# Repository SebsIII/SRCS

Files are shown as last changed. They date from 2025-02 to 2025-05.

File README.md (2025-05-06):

# SRCS - Satellite Receiver Control Station

The Satellite Receiver Control Station (SRCS) is an operational facility dedicated to maximizing the quality and reliability of satellite signal reception. This is achieved through the continuous acquisition, processing, and analysis of diverse sensor data streams. The SRCS leverages this information to dynamically optimize antenna pointing, receiver parameters, and other system configurations, ensuring optimal signal capture and data integrity.

## Description
The control station is made primarely of 2 modules:
- The motorized antenna module : The **core** of the control station and the actual receiver, it's composed of a [Vee dipole antenna](https://en.wikipedia.org/wiki/Dipole_antenna) tuned at NOAA's frequencies in horizontal polarization and connected to a [28BYJ-48](https://www.mouser.com/datasheet/2/758/stepd-01-data-sheet-1143075.pdf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) stepper motor, which handles it's ability to rotate the antenna to track satellites.
- The weather data module - The secondary part of the SRCS that gathers weather data that will be analyzed by the [MCU](https://en.wikipedia.org/wiki/Microcontroller) and saved on an external database.
## 🛰️ The NOAA's satellites

The NOAA ([National Oceanic Atmospheric Atministration](https://www.noaa.gov/)) is a US  agecy that studies how weather changes our planet, both on it's surface and under the seas. <br>
Other then other missions, it made a [campaign of polar-orbiting, non-geosynchronous, environmental satellites](https://www.n2yo.com/satellites/?c=4), from NOAA-1 up to NOAA-21. <br>
From all of those, the best and easiest one to receive are the NOAA-15, NOAA-18 and NOAA-19, which continously trasmit weather data with [APT](https://en.wikipedia.org/wiki/Automatic_picture_transmission) techniques on their downlink frequency as a "sound". <br>
Those "sounds" will eventually need to be converted into .WAV files and thed decoded with an apt-decoder, in our case we'll use [noaa-apt](https://noaa-apt.mbernardi.com.ar/).

<table>
<tr><td>Name</td><td>NORAD ID</td><td>Freq MHz</td></tr>
<tr><td>NOAA 15</td><td><a href="https://www.n2yo.com/satellite/?s=25338">25338</a></td><td>137.620</td></td></tr>
<tr><td>NOAA 18</td><td><a href="https://www.n2yo.com/satellite/?s=28654">28654</a></td><td>137.9125</td></tr>
<tr><td>NOAA 19</td><td><a href="https://www.n2yo.com/satellite/?s=33591">33591</a></td><td>137.1</td></tr>
</table>

## 1st Module: The Vee Dipole Antenna

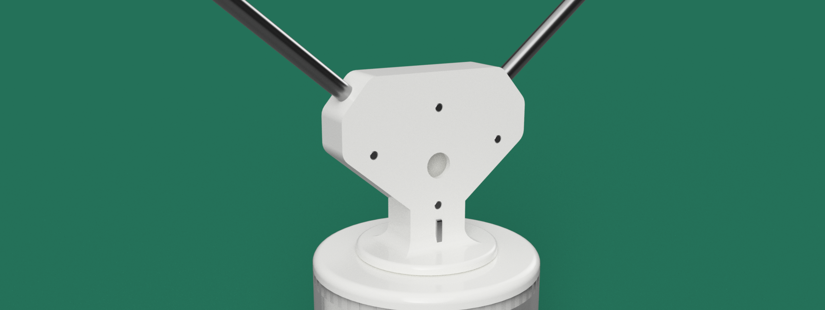
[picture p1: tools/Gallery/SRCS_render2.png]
Vee antenna


The first module is made of two parts, the **dipole antenna** and the **motorized support**:
- The dipole antenna is the effective receiver of the SRCS, it's a horizontally polazied, omnidirectional, **Vee dipole antenna** tuned at 137.25 MHz (average downlink frequency of NOAA-15,18,19 *). <br>
  The antenna output will eventually be connected to a 50 ohm [RG58 coaxial cable](https://www.farnell.com/datasheets/2095749.pdf) that will transfer the output signal from the antenna to the [RTL-SDR](https://en.wikipedia.org/wiki/Software-defined_radio) or the general receiver that will, later on, analyze the signal and convert it in an image. <br>
  
- The motorized support is where the antenna is mounted and the part that will, indeed, **rotate** the antenna itself while the satellite is passing near the SRCS 
  to ensure the highest quality receiving of data reception of the dipole. <br>
  Its mainly composed of a [28BYJ-48 stepper motor](https://www.mouser.com/datasheet/2/758/stepd-01-data-sheet-1143075.pdf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), a **5.625:1 gear box** to reduce the motor speed and to reduce the minimum step angle and an [AS5600 magnetic encoder](https://files.seeedstudio.com/wiki/Grove-12-bit-Magnetic-Rotary-Position-Sensor-AS5600/res/Magnetic%20Rotary%20Position%20Sensor%20AS5600%20Datasheet.pdf) to get the exact rotation angle of the dipole.
  
<h6>* The bandwidth of the 137.25 MHz dipole antenna offers enough bandwindth to get all the 137.1, 137.620 and 137.9125 MHz frequencies </h6>

## 2nd Module: Weather data Module

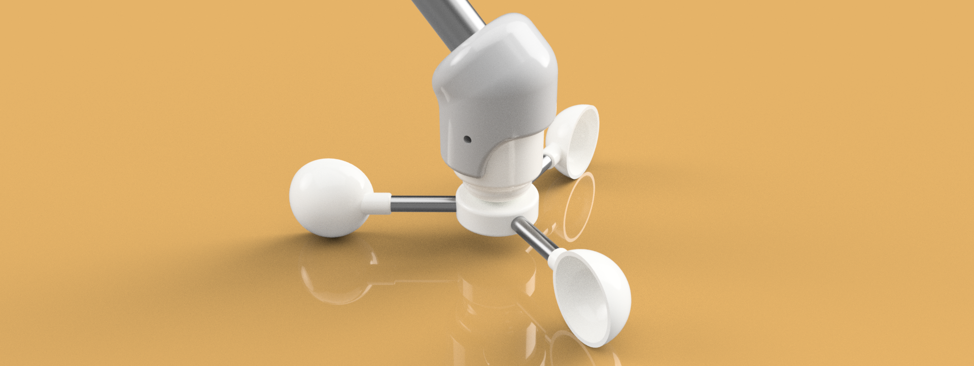
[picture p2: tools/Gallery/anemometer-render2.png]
anemometer


The second module is the weather monitor system, which is the part which goal is to gather weather data that will later on, be analyzed by the MCU.
It's composed of various sensors, including: [DHT11]() for **temperature and humidity**, a light sensor, to gather **ambient light level**, an anemometer for **wind speed** and a rain sensor. <br>
The combination of those data, will be used to **monitor and predict how currend and future weather is/will be**. <br>
Those info are necessary to better understand how the weather will be during the NOAA receiving sessions, since those conditions can impact on the reciving quality and/or damage some components if used under certain situations, like rain or extreme wind storms.

## The Power Managment System PMS

The SRCS is powered by a **9v 5w solar panel** which charges up a **12v 7AH Lead acid battery** with a **[XY-L10A](https://www.google.com/url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) BMS** which handles and manages the battery charging-sequencies.
Before the BMS, there's a **buck step-up circuit** which up-shifts the voltage from *9v => ~13v*, needed to charge the battery.
The battery outputs are then inputted in two **buck step-down circuits**, one at *~7,5v for the MCU power supply* and the other at *5v for the sensors power supply*.

The complete system is schematized below:

``` 
Solar panel
    |        
    v        
   13v---> XY-L10A
    |        v
    v        |
 Battery <---/
  |   |
  v   v
 7.5v 5v--> Sensors IN 
  |
  v   
STM32F401RE VIN
```

## The communication protocol

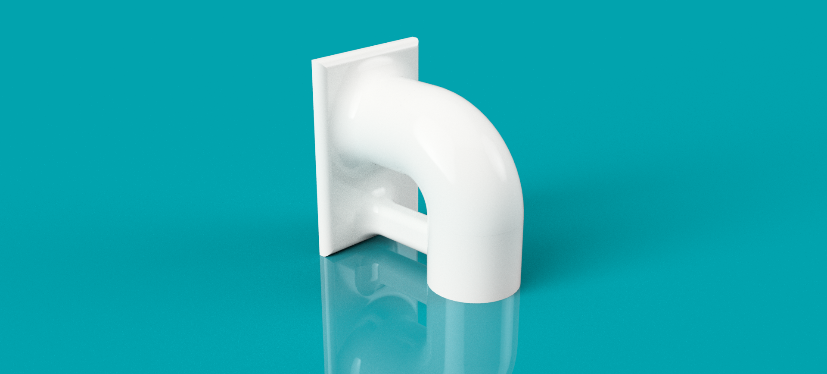
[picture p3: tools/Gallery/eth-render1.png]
dashboard-overview


The SRCS, other than a control station is also a **web server** hosting a **local website**, on which are displayed the weather data, the SRCS status, the nearby satellite passes data and much more.
 
The website is written in **HTML**,**CSS** and **JS** and the communication protocol between the website and the SRCS itself is based on [AJAX](https://en.wikipedia.org/wiki/Ajax_(programming)).

The **website local IP address** is set to:
```
http://192.168.1.100
```

## Usage

When you want to start a new reception session, click the **Start reception session** button, a login pop-up will show up, in this, you will need to insert the password to continue. 

If the password is right, a new pop-up will show up, requesting the **command info to send to the SRCS**, The command is in this format:
``` 
Rotate [from] degrees => [to] degrees in [for] seconds, [after] seconds
```

here's an *example* to better understand how the command format works:
> Rotate from 0° => to 180°, in 600s, after 900s 

With this command, the SRCS will **align and rotate the antenna from 0° [North] to 180° [south] in 10 min, after 15min after the reception of the command**.

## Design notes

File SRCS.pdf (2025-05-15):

Cutillo Sebastiano Maria - A.S. 2024/2025

## SRCS - Satellite Receiver Control Station

https://github.com/SebsIII/SRCS

La Satellite Receiver Control Station (SRCS) è una struttura operativa dedicata a massimizzare la qualità e l'affidabilità della ricezione dei segnali satellitari. Questo obiettivo viene raggiunto attraverso l'acquisizione, l'elaborazione e l'analisi continua di diversi flussi di dati da sensori.

La SRCS sfrutta queste informazioni per ottimizzare dinamicamente il puntamento dell'antenna, i parametri del ricevitore e altre configurazioni del sistema, garantendo la cattura ottimale del segnale e l'integrità dei dati.

Descrizione

La stazione di controllo è composta principalmente da 2 moduli:

- Il modulo antenna motorizzata: il cuore della stazione di controllo e del ricevitore vero e proprio, è composto da un'antenna dipolo Vee sintonizzata sulle frequenze NOAA in polarizzazione orizzontale e collegata a un motore passo-passo 28BYJ-48, che ne gestisce la capacità di ruotare l'antenna per seguire i satelliti.
- Il modulo dati meteo - La parte secondaria dell'SRCS che raccoglie i dati meteo che saranno analizzati dalla MCU e salvati su un database esterno.

I satelliti NOAA

La NOAA (National Oceanic Atmospheric Atministration) è un'agenzia statunitense che studia come le condizioni meteorologiche modificano il nostro pianeta, sia sulla superficie che sotto i mari. Oltre ad altre missioni, ha realizzato una campagna di satelliti ambientali in orbita polare, non geosincroni, dal NOAA-1 fino al NOAA-21.

Di tutti questi, i migliori e più facili da ricevere sono i NOAA-15, NOAA-18 e NOAA-19, che trasmettono continuamente dati meteorologici con tecniche APT sulla loro frequenza di downlink come “suono”.

Questi “suoni” dovranno essere convertiti in file .WAV e decodificati con un decodificatore apt.

1° Modulo: L'antenna a dipolo Vee

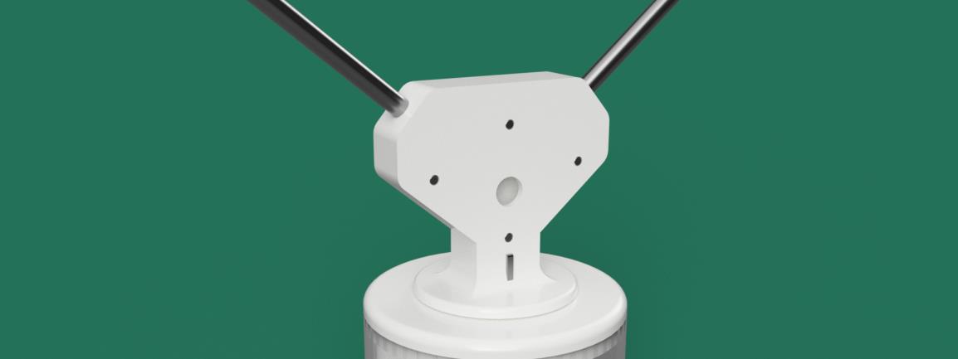
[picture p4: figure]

Il primo modulo è composto da due parti, l'antenna a dipolo e il supporto motorizzato:

- L'antenna a dipolo è il ricevitore effettivo dell'SRCS; si tratta di un'antenna a dipolo Vee, omnidirezionale e polarizzata orizzontalmente, sintonizzata a 137,25 MHz (frequenza media di downlink delle NOAA-15,18,19 *). L'uscita dell'antenna sarà infine collegata a un cavo coassiale RG58 da 50 ohm che trasferirà il segnale in uscita dall'antenna all'RTL-SDR o al ricevitore generale che, in seguito, analizzerà il segnale e lo convertirà in un'immagine.
- Il supporto motorizzato è il punto in cui viene montata l'antenna e la parte
che, di fatto, ruoterà l'antenna stessa mentre il satellite passa vicino all'SRCS per garantire la massima qualità di ricezione dei dati del dipolo. È composto principalmente da un motore passo-passo 28BYJ-48, una scatola di ingranaggi 5,625:1 per ridurre la velocità del motore e ridurre l'angolo di passo minimo e un encoder magnetico AS5600 per ottenere l'angolo di rotazione esatto del dipolo.

* La larghezza di banda dell'antenna a dipolo da 137,25 MHz offre una banda sufficiente per ottenere tutte le frequenze di 137,1, 137,620 e 137,9125 MHz.

2° Modulo: Modulo dati meteo

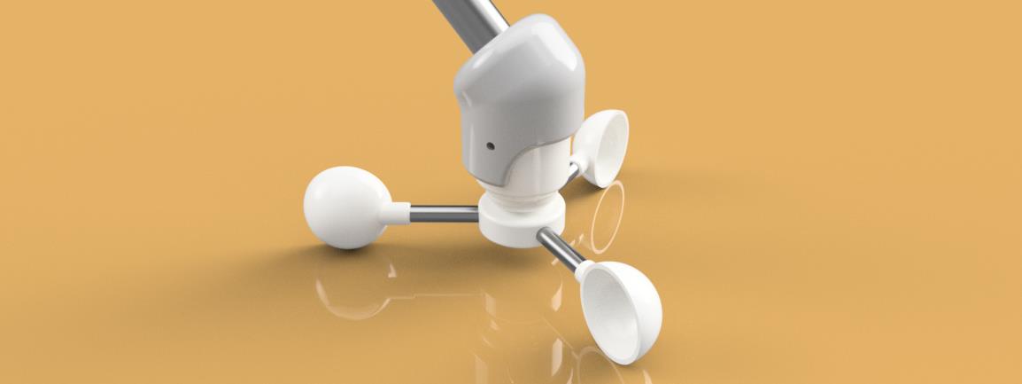
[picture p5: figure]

Il secondo modulo è il sistema di monitoraggio meteorologico, ovvero la parte che ha lo scopo di raccogliere i dati meteorologici che saranno poi analizzati dall'MCU. È composto da vari sensori, tra cui: DHT11 per la temperatura e l'umidità, un sensore di luminosità, per raccogliere il livello di luce ambientale, un anemometro per la velocità del vento e un sensore di pioggia.

La combinazione di questi dati sarà utilizzata per monitorare e prevedere l'andamento e le condizioni meteorologiche future.

Queste informazioni sono necessarie per comprendere meglio le condizioni meteorologiche che si verificheranno durante le sessioni di ricezione NOAA, poiché tali condizioni possono influire sulla qualità della ricezione e/o danneggiare alcuni componenti se utilizzati in determinate situazioni, come pioggia o tempeste di vento estreme.

Il sistema di gestione dell'energia PMS

Il sistema di gestione dell'alimentazioneL'SRCS è alimentato da un pannello solare da 9v 5w che carica una batteria al piombo da 12v 7AH con un BMS XY-L10A che gestisce le sequenze di carica della batteria. Prima del BMS, c'è un circuito buck step-up che aumenta la tensione da 9v => ~13v, necessaria per caricare la batteria. Le uscite della batteria vengono poi immesse in due circuiti buck step-down, uno a ~7,5v per l'alimentazione della MCU e l'altro a 5v per l'alimentazione dei sensori.em PMS

Il protocollo di cominicazione

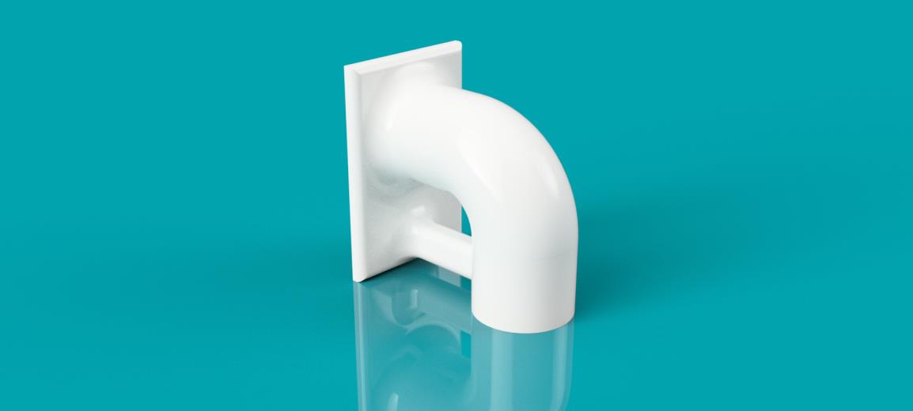
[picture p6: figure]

L'SRCS, oltre a essere una stazione di controllo, è anche un server web che ospita un sito web locale, sul quale vengono visualizzati i dati meteo, lo stato dell'SRCS, i dati dei passaggi dei satelliti nelle vicinanze e molto altro.

Il sito web è scritto in HTML, CSS e JS e il protocollo di comunicazione tra il sito web e l'SRCS stesso è basato su AJAX.

L'indirizzo IP locale del sito è impostato su: 192.168.1.100

Utilizzo

Quando si desidera avviare una nuova sessione di ricezione, fare clic sul pulsante Avvia sessione di ricezione; viene visualizzato un pop-up di accesso, in cui è necessario inserire la password per continuare.

Se la password è corretta, viene visualizzato un nuovo pop-up che richiede le informazioni sul comando da inviare all'SRCS:

Ruota [da] gradi => [a] gradi in [per] secondi, [dopo] secondi

Ecco un esempio per capire meglio come funziona il formato del comando:

Ruota da 0° => a 180°, in 600s, dopo 900s

Con questo comando, l'SRCS allineerà e ruoterà l'antenna da 0° [nord] a 180° [sud] in 10 minuti, dopo 15 minuti dalla ricezione del comando.

GitHub

Per maggiori informazioni, il codice completo, le immagini ed altro, il progetto si trova su GitHub al link: https://github.com/SebsIII/SRCS

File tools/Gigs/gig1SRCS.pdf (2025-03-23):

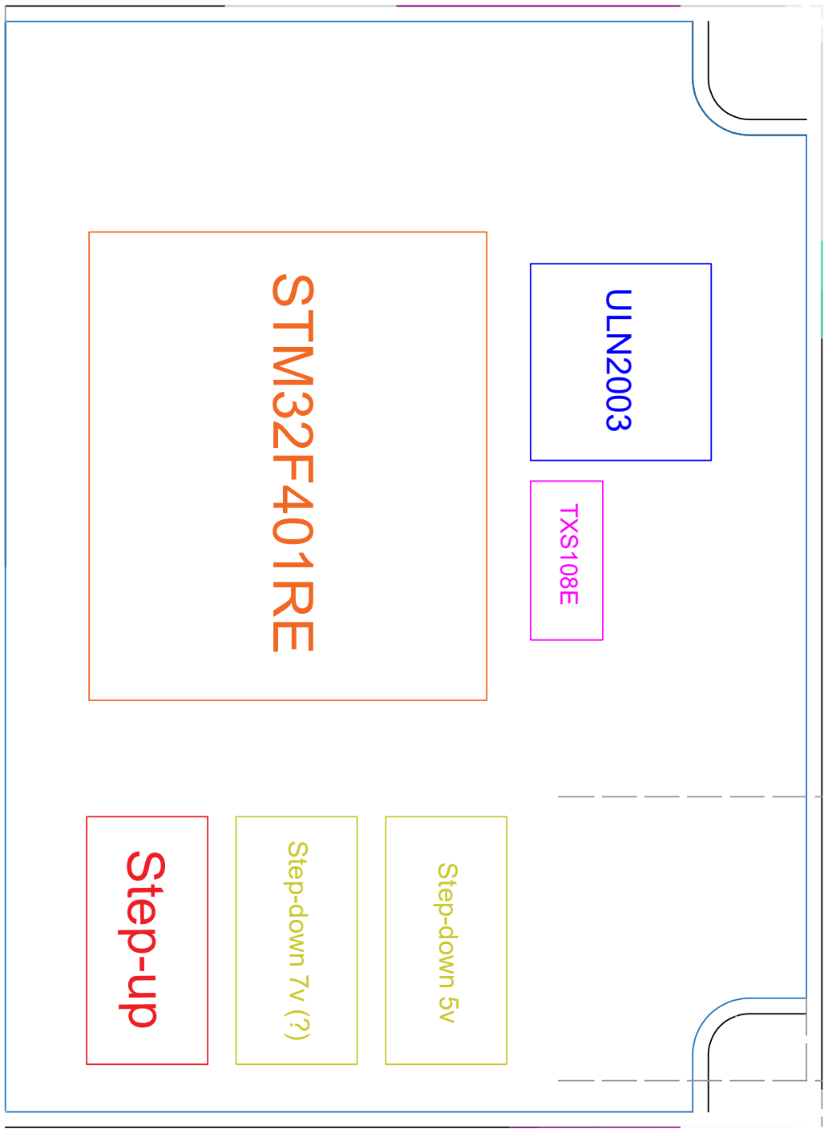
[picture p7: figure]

STM32F401RE Step-up Step-down 7v (?) Step-down 5v ULN2003 TXS108E

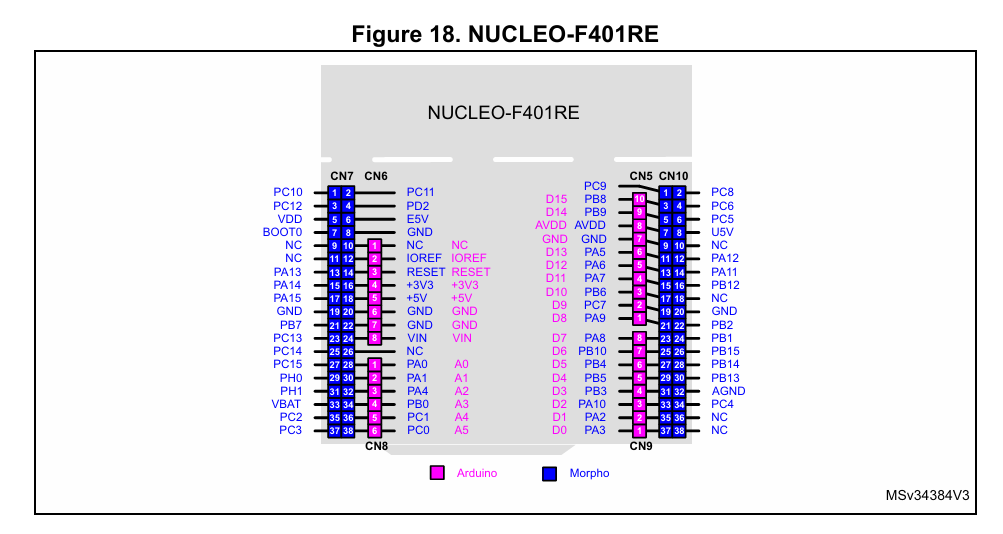
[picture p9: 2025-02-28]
datasheets/F401RE-pinout.png

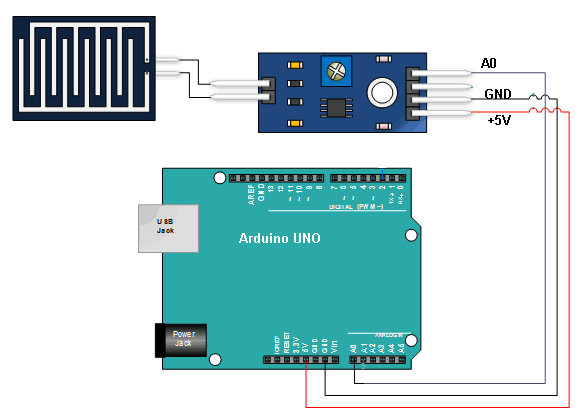
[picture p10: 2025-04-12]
wireups/Rain-sensor-wireup.png

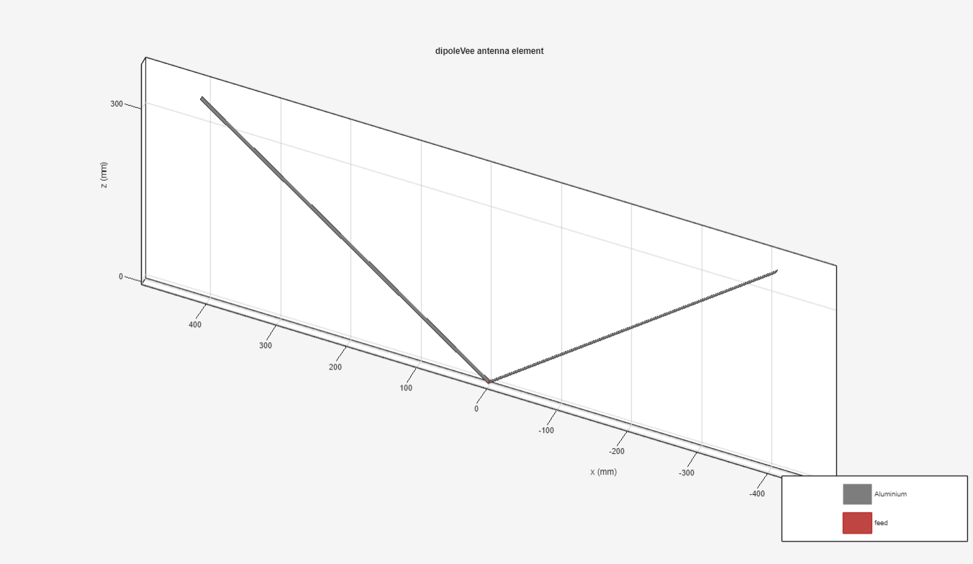
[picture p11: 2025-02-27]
datasheets/Vee-antenna/antenna-V.png

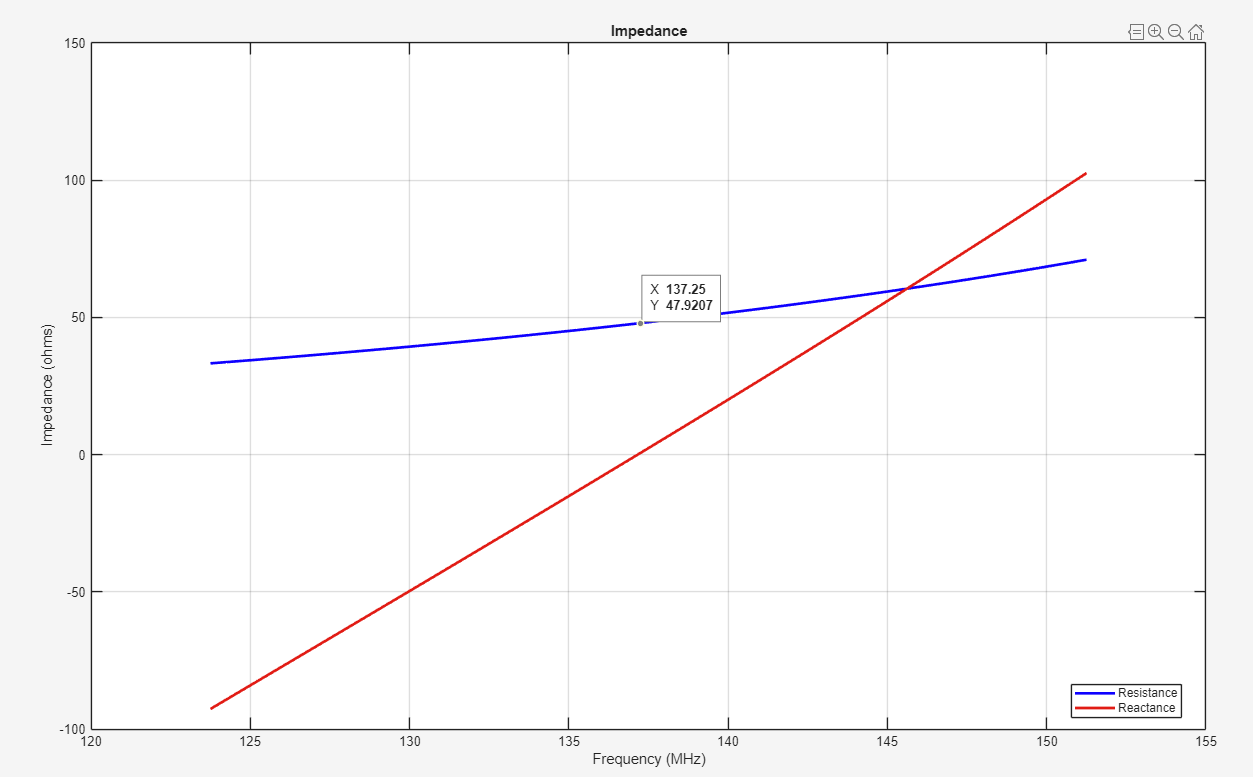
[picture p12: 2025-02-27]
datasheets/Vee-antenna/impedance.png

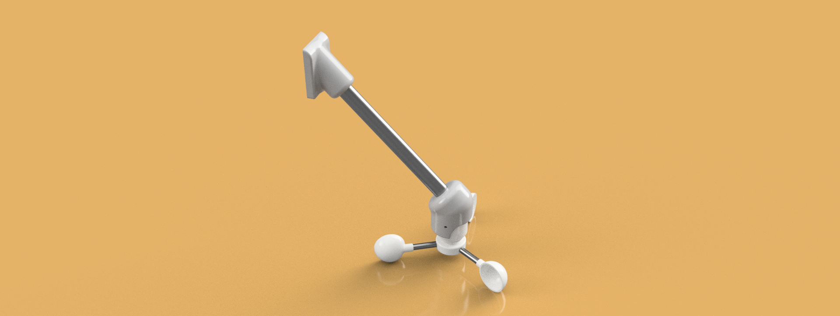
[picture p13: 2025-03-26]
tools/Gallery/anemometer-render1.png

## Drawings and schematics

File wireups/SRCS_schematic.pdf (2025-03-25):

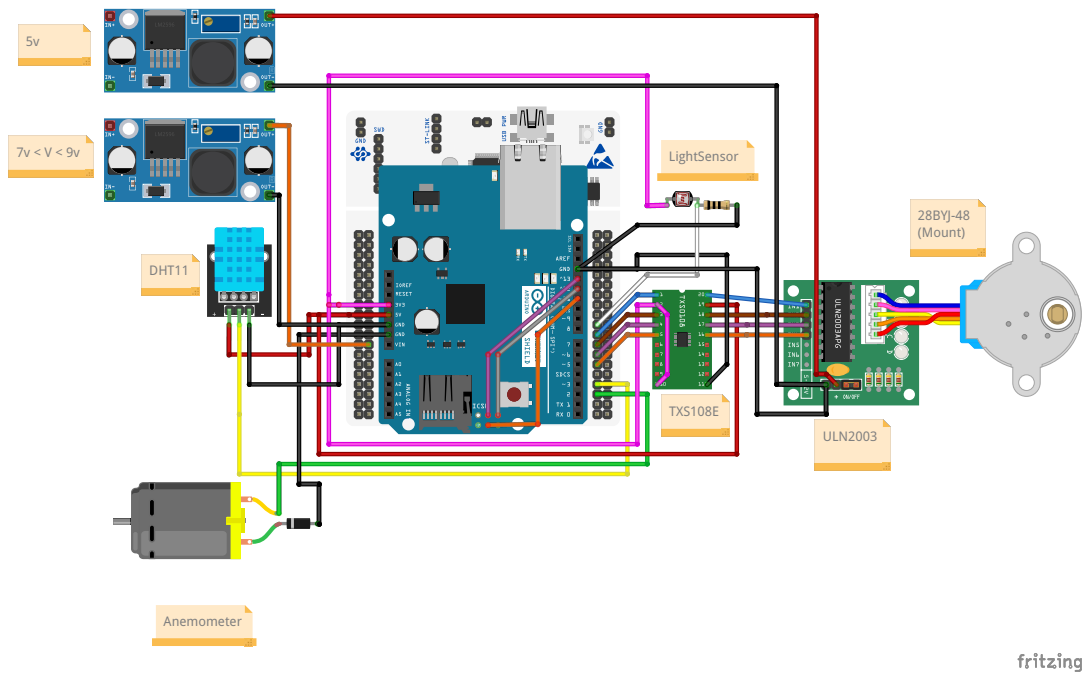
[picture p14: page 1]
Anemometer; DHT11; LightSensor; TXS108E; ULN2003; 28BYJ-48 (Mount)

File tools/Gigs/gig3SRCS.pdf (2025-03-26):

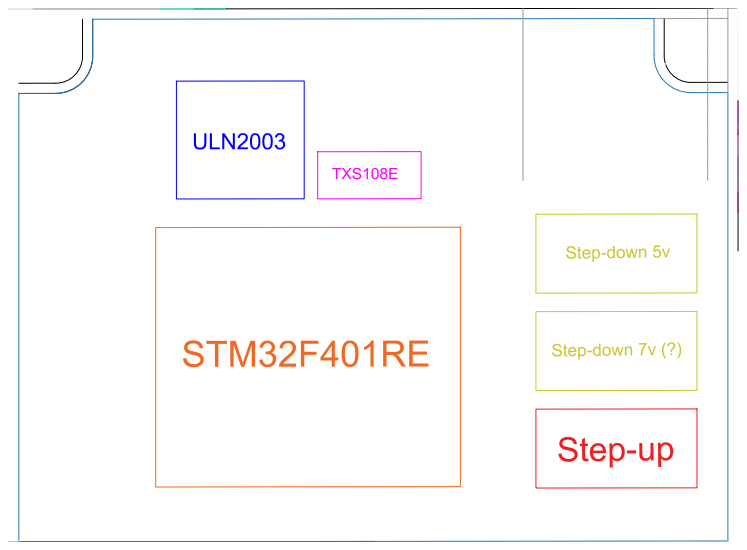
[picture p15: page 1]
STM32F401RE; Step-up Step-down 7v (?) Step-down 5v ULN2003; TXS108E

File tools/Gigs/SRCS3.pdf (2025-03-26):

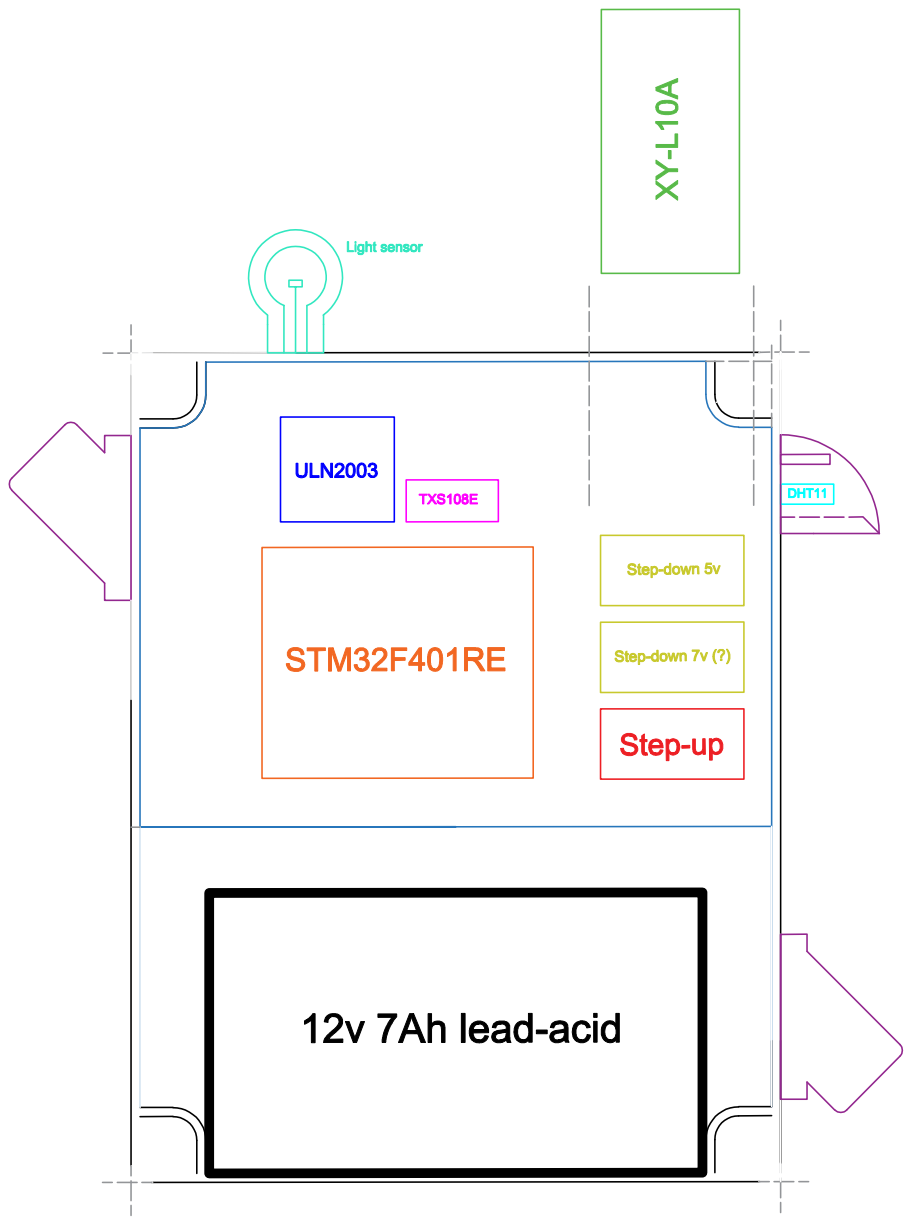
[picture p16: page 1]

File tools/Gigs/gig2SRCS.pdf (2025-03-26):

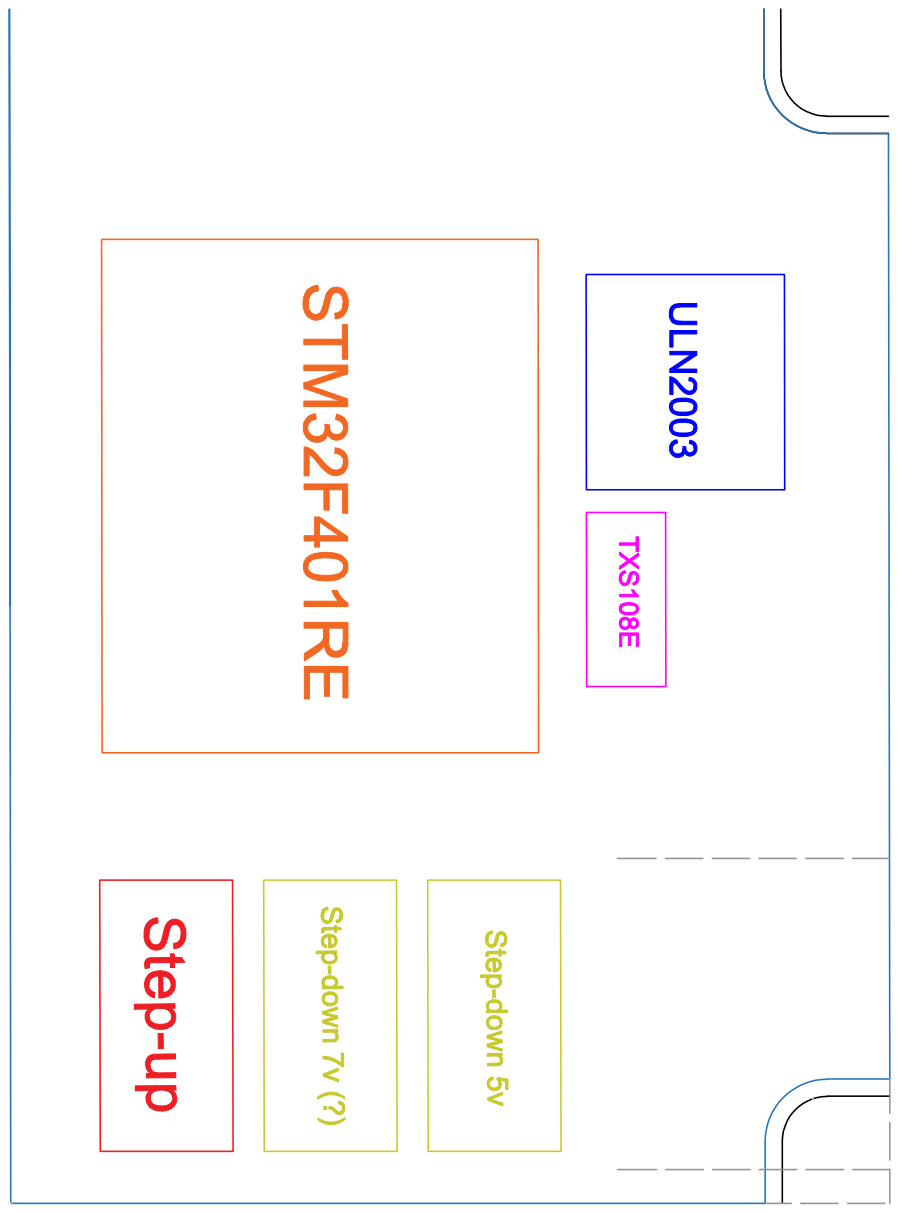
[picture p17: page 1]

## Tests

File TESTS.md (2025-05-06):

# SENSORS' TESTS

- [X] TXS0108E
- [x] 28BYJ-48
- [x] ULN2003
- [X] rain sensor
- [X] DHT11 - OK
- [X] Photoresistor
- [X] W5100 

## WIREUPS

- [X] [STM32 TO ARDUINO IDE](https://www.youtube.com/watch?v=yssEiMLGH90)
- [X] [DHT11](https://randomnerdtutorials.com/esp32-dht11-dht22-temperature-humidity-sensor-arduino-ide/), adapted
- [X] [STM32 to Ethernet shield](https://balau82.wordpress.com/2015/08/02/arduino-ethernet-shield-on-stm32-nucleo/)
- [ ] [AJAX](https://startingelectronics.org/tutorials/arduino/ethernet-shield-web-server-tutorial/web-server-read-switch-using-AJAX/)
- [X] [Ajax sd web](https://www.youtube.com/watch?v=E3uCFFf3hxc)

## Snippets

Pin Format: NAMEPIN

### DHT11

``` cpp
float getTemperature(){
  float T = dht.readTemperature();
  if (isnan(T)) {   
    return 0;
  }
  return  T;
}
```
``` cpp
float getHumidity(){
  float H = dht.readHumidity();
  if (isnan(H)) {   
    return 0;
  }
  return  H;
}
```

## Rain Sensor
``` cpp
int getRain(){  //To format raw input 
  int RL = analogRead(RAINPIN);
  return  RL;
}
```

## Light Sensor
``` cpp
int getLight(){  //To format raw input 
  int LL = analogRead(PHOTOPIN);
  return  LL;
}
```

## Anemometer
``` cpp
float getWind(){  //To format raw input (?)
  int WS = analogRead(ANEMOPIN);
  return  WS;
}
```

## Rain A => value
- 1020~1023 = clear
- 1019~800 = some droplets
- 799~600 = rain
- 599~50 = heavy rain
- 50~0 = metal on the sensor

## Web datasheet
- **AA** - Antenna Azimuth
- **AD** - [Last] Antenna Direction
- **MApDR** - Maximum Angle per Direction (of) Rotation [left]
- **Rain** - Rain Level
- **POST** - [Last] Power On Self Test [Outcome]
- **MRC** - Meteorological Reliability Coefficient

## Web data
- font - [Questial, allura, Oswald]

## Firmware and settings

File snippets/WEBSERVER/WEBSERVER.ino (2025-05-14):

/*
  SRCS basecode by Sebs_

  This is the source code for SRCS MCU, it handles HTTPreq from clients,
  stores and hosts a web server and does calculations in order to get,
  analyze and send the sensors' data to each client.

  Documentation and assets: https://github.com/SebsIII/SRCS

*/
#include <SPI.h>
#include <Ethernet.h>
#include <SD.h>
#include <DHT.h>
#include "AS5600.h"
#include <Stepper.h>

#define DHTPIN 3
#define DHTTYPE DHT11

#define PHOTOPIN A0
#define RAINPIN A1 
#define ANEMOPIN A2

AS5600 as5600;
Stepper mount(64, 8,6,7,5);
DHT dht(DHTPIN, DHTTYPE);
File HMTL_file, pswLog_file;

String psw, pswAttempt, alignCmmd;
int align_from = -1, align_to = -1, align_for =-1, align_after = -1, from_value, to_value, for_value, after_value ;
int startPoint, endPoint;
int dataArray[4];
float weatherData[5];
bool haveJob = false;
unsigned long instantTime, lastTrigger = 0, jobTime;
int isClockwise = 1; //1 = counter clock-wise, -1 = clok-wise
byte mac[] = {
  0xDE, 0xAD, 0xBE, 0xEF, 0xFE, 0xED
};
IPAddress ip(192, 168, 1, 100); 
EthernetServer server(80);

void setup()
{
  Serial.begin(115200);
  pinMode(PHOTOPIN, INPUT);
  pinMode(RAINPIN, INPUT);
  pinMode(ANEMOPIN, INPUT);
  if(!POST()){
    Serial.println("POST FALSE");
    while (true){};
  }
  
  pswLog_file = SD.open("psw.txt");
  while (pswLog_file.available()){
    psw += (char)pswLog_file.read();
  }

}

void loop()
{
  String HTTP_req;
  EthernetClient client = server.available();
  
  if(client)
  {
    boolean currentLineIsBlank = true;
    while (client.connected())
    {
      instantTime = millis()/1000;
      if(instantTime%1 == 0 && instantTime != lastTrigger){
        lastTrigger = instantTime;
        checkAndExecJob();
      }
      
      if(client.available())
      { 
        char c = client.read();
        HTTP_req += c;
        if(c == '\n' && currentLineIsBlank)
        {
          //-------------------------------------------------------------------
          if(HTTP_req.indexOf("getWeather")>-1)
          {
            weatherData[0] = getTemperature();
            weatherData[1] = getHumidity();
            weatherData[2] = getLight();
            weatherData[3] = getWind();
            weatherData[4] = getRain();

            client.println("HTTP/1.1 200 OK");
            client.println("Content-Type: text/plain");
            client.println("Connection: close");
            client.println();
            client.print('[');
            for (int i = 0; i < 5; i++){
              client.print(weatherData[i]);
              if (i != 4){
                client.print(',');
              }
            }
            client.println(']');  
            
          }
          else if(HTTP_req.indexOf("readGENERAL")>-1)
          {
            client.println("HTTP/1.1 200 OK");
            client.println("Content-Type: text/plain");
            client.println("Connection: close");
            client.println();
            client.println(as5600.rawAngle() * AS5600_RAW_TO_DEGREES);
            //MApDR als
          }
          else if(HTTP_req.indexOf("alignAntennaTo0")>-1)
          {
            client.println("HTTP/1.1 200 OK");
            client.println("Content-Type: text/plain");
            client.println("Connection: close");
            client.println();

            alignTo(0);
            client.print("Antenna-algned,isClockwise:");
            client.println(isClockwise);
            isClockwise = 1;
          }
          else if(HTTP_req.indexOf("pswReq")>-1)
          {
            Serial.println("psw requested.");
            for (int i = HTTP_req.indexOf("pswReq/"); i < HTTP_req.length(); i++){
              if(HTTP_req[i] == '/'){
                  int c = i + 1;
                  while(HTTP_req[c] != ' '){
                    pswAttempt += HTTP_req[c];
                    c++;
                  }
                  break;
              }
            }
            client.println("HTTP/1.1 200 OK");
            client.println("Content-Type: text/plain");
            client.println("Connection: close");
            client.println();
            int c = 0;
            for(int i = 0; i < psw.length(); i++){
              Serial.print(pswAttempt[i]);
              Serial.println(psw[i]);
              if(pswAttempt[i] == psw[i]){
                c++;
              }
            }
            if (c == psw.length() - 1 && pswAttempt.length() == psw.length() - 1)
            {
              client.println("true");
            } else {
              client.println("false");
            }
            pswAttempt = "";
            
            
          }
          else if(HTTP_req.indexOf("alignCmmd")>-1)
          {
            Serial.println("Antenna align requested.");

            for (int i = HTTP_req.indexOf("alignCmmd") + 9; i < HTTP_req.length(); i++){
              if(HTTP_req[i] != ' '){
                alignCmmd += HTTP_req[i];
              }else{
                break;
              }
            }
            
            char buffer[30];
            alignCmmd.toCharArray(buffer, 30);
            char *token = strtok(buffer, "/");

            int j = 0;
            while (token != NULL) {
              dataArray[j] = atoi(token);
              token = strtok(NULL, "/");
              j++;
            }

            for(int i = 0; i < 4; i++){
              Serial.println(dataArray[i]);
            }
            Serial.println("-----");

            haveJob = true;
            Serial.print(dataArray[3]);
            jobTime = millis() + (dataArray[3] * 1000UL);
            Serial.print("Job time is: ");
            Serial.print(jobTime);
            Serial.print(" - ");
            Serial.println(millis());
  


            client.println("HTTP/1.1 200 OK");
            client.println("Content-Type: text/plain");
            client.println("Connection: close");
            client.println();
            client.println("test concluded.");
            
            memset(buffer, 0, sizeof(buffer));
            alignCmmd = "";
            //print something that comunicates the reception, then process cmmd
            
          }
          //-------------------------------------------------------------------
          else
          {
            client.println("HTTP/1.1 200 OK");
            client.println("Content-Type: text/html");
            client.println("Connection: close");
            client.println();
            HMTL_file = SD.open("index.htm");
            if(HMTL_file)
            {
              while(HMTL_file.available()) client.write(HMTL_file.read());
              HMTL_file.close();
            }
          }
          //-------------------------------------------------------------------
          //HTTP_req = "";
          break;
        }
        //---------------------------------------------------------------------
        if(c == '\n') currentLineIsBlank = true;
        else if(c != '\r') currentLineIsBlank = false;
      }
    }
    delay(10);
    client.stop();
    //haveJob = false;
    //Serial.println("Client quitted - all jobs aborted.");
  }
}

float getTemperature(){
  float T = dht.readTemperature();
  if (isnan(T)) {   
    return 0;
  }
  return  T;
}

float getHumidity(){
  float H = dht.readHumidity();
  if (isnan(H)) {   
    return 0;
  }
  return  H;
}

float getLight(){
  int LL = analogRead(PHOTOPIN);
  return  LL;
}

float getRain(){ 
  int RL = analogRead(RAINPIN);
  return  RL;
}

float getWind(){
  int WS = analogRead(ANEMOPIN);
  return  WS;
}

void checkAndExecJob(){
  int currentTime = millis();
  Serial.println(currentTime);
  if (haveJob == true)
  {
    bool isAligned = false;
    Serial.println("There's a job active.");
    if (currentTime >= jobTime)
    {
      Serial.println("The time has come.");
      int currentPos = as5600.rawAngle() * AS5600_RAW_TO_DEGREES;
      if(currentPos <= dataArray[0]+1 || currentPos >= dataArray[0]-1){
        //start reception
        /*
        angle/time = angle/s;
        i can make a function that rotates of a degree and use a delay to move at the right time?
        */

        float currentPos = as5600.rawAngle() * AS5600_RAW_TO_DEGREES;
        int targetAz = dataArray[1];
        mount.setSpeed(80);
        mount.step(-40.63);
        float newPos = as5600.rawAngle() * AS5600_RAW_TO_DEGREES;
        Serial.print("degree per 10 steps: ");
        Serial.println(newPos-currentPos);
        Serial.print("steps per degree: ");
        Serial.println(1/((newPos-currentPos)/50));


      } else {
        Serial.println("Antenna is not aligned.");
      }
    
   }
    else if ((jobTime-currentTime)/1000 <= 60)
    {
      Serial.println("T-60, aligning antenna.");
      if(alignTo(dataArray[0])){
        isAligned = true;
        Serial.print("aligned to: ");
        Serial.println(dataArray[0]);
      } else {
        Serial.println("error during aligning session.");
      }
      
    }
  }
}

bool alignTo(int targetAz){
  bool isAligned = false;
  int currentPos = as5600.rawAngle() * AS5600_RAW_TO_DEGREES;
  mount.setSpeed(80); //adjust if too much
  if(currentPos > 180){
    isClockwise = -1;
  }
  while (!isAligned){  
    if(currentPos == targetAz){
      isAligned = true;   
    } else{
      mount.step(isClockwise * 30);
      delay(50);
      Serial.print(as5600.rawAngle());    //DEL
      Serial.print(" - ");    //DEL
      Serial.println(currentPos);   //DEL
      currentPos = as5600.rawAngle() * AS5600_RAW_TO_DEGREES;
    }
    Serial.println(isAligned);    //DEL
  }
  isAligned = false;
  return true;
}

bool POST(){
  if(SD.begin(4)){
    if(SD.exists("index.htm")){
      if(SD.exists("psw.txt")){
        Ethernet.init(10);
        Ethernet.begin(mac, ip);
        server.begin();
        dht.begin();
        Wire.begin();
        as5600.setDirection(AS5600_CLOCK_WISE);
        return true;
      } else {
        return false;
      }
    } else{
      return false;
    }
  } else{
    return false;
  }
}

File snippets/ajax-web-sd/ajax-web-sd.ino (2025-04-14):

//-----------------------------------------
//Arduino DHT11 Web Server using AJAX
//HTML code of webpage is stored on SD card
//-----------------------------------------
#include <SPI.h>
#include <Ethernet.h>
#include <SD.h>
#include <DHT.h>
//------------------------------------------------

#define DHTPIN 3
#define DHTTYPE DHT11

DHT dht(DHTPIN, DHTTYPE);
File HMTL_file;
//------------------------------------------------
byte mac[] = {
  0xDE, 0xAD, 0xBE, 0xEF, 0xFE, 0xED
};
IPAddress ip(192, 168, 1, 100); 
EthernetServer server(80);
//==================================================================================
void setup()
{
  Serial.begin(9600);
  dht.begin();
  //pinMode(53, OUTPUT);
  //-----------------------------------------------------
  Serial.println(F("Initializing SD card..."));
  if(!SD.begin(4))
  {
    Serial.println(F("Initialization failed!")); return;
  }
  Serial.println(F("Initialization OK"));
  //-----------------------------------------------------
  if(!SD.exists("index.htm"))
  {
    Serial.println(F("index.htm not found!")); return;
  }
  Serial.println(F("index.htm found"));
  //-----------------------------------------------------
  Ethernet.init(10);
  Ethernet.begin(mac, ip);
  server.begin();
  Serial.print(F("Server Started...\nLocal IP: "));
  Serial.println(Ethernet.localIP());
}
//==================================================================================
void loop()
{
  String HTTP_req;
  EthernetClient client = server.available();
  //---------------------------------------------------------------------------
  if(client)
  {
    boolean currentLineIsBlank = true;
    while (client.connected())
    {
      if(client.available())
      { 
        char c = client.read();
        HTTP_req += c;
        if(c == '\n' && currentLineIsBlank)
        {
          client.println("HTTP/1.1 200 OK\n\rContent-Type: text/html\n\r\n\r");
          //-------------------------------------------------------------------
          if(HTTP_req.indexOf("readDHT11")>-1)
          {
            client.println("Temp&nbsp;&nbsp;&nbsp;&nbsp;: ");
            client.println(dht.readTemperature());
            client.println("°C<br>Humidity:&nbsp;&nbsp;&nbsp;");
            client.println(int(dht.readHumidity()));
            client.println("&nbsp;%");
          }
          //-------------------------------------------------------------------
          else
          {
            HMTL_file = SD.open("index.htm");
            if(HMTL_file)
            {
              while(HMTL_file.available()) client.write(HMTL_file.read());
              HMTL_file.close();
            }
          }
          //-------------------------------------------------------------------
          //HTTP_req = "";
          break;
        }
        //---------------------------------------------------------------------
        if(c == '\n') currentLineIsBlank = true;
        else if(c != '\r') currentLineIsBlank = false;
      }
    }
    delay(10);
    client.stop();
  }
}

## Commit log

2025-04-12 Rain wireup image uploaded
2025-04-14 Shit, last commit, same thing
    Last one was the wrong one :/
    [WEBSERVER.ino]
2025-04-14 Uploaded eth support gcode to be printed
2025-04-15 fixed some bugs, added features made new functions
    [WEBSERVER.ino]
2025-04-17 Update WEBSERVER.ino
    Missed a letter "readL" => "readR"
    line 93
    [WEBSERVER.ino]
2025-05-06 updated features, cometed N2YO, fixed bugs
    [WEBSERVER.ino]
2025-05-07 updated alignCmmd, still to fix
    [WEBSERVER.ino]
2025-05-07 added bugs, WHILE UNSTABLE
    [WEBSERVER.ino]
2025-05-14 added features, fixed bugs, continued alignCmmd functions
    [WEBSERVER.ino]
